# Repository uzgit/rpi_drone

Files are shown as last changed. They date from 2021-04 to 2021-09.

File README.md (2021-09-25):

# Raspberry Pi Drone

This is designed for a Navio2 + RPi flight controller and a power system similar to the [DJI Snail](https://www.dji.com/snail) with a 3S (11.1V) LiPo. It is a modified version of the drone found [on Thingiverse here](https://www.thingiverse.com/thing:2269010).

It is particularly good for scenarios with potentially rough landings, as it is flexible enough to ragdoll a bit, while being strong enough to fly nicely.

## Initialization (if you want to edit or re-generate files):
* Install OpenSCAD: `sudo apt-get install openscad`
* Clone the repo to your computer.
* Run the `./build.sh` script (make sure you have OpenSCAD installed or else this step will obviously not work).

## Printing (drone with gimbal):

Print Item | Quantity | File | Image
:-: | :-: | :-: | :-: |
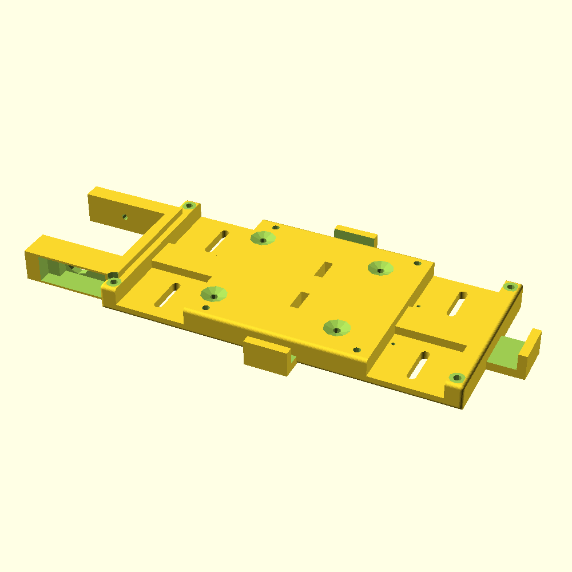
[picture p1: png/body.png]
Body | 1 | `stl/body.stl` | 
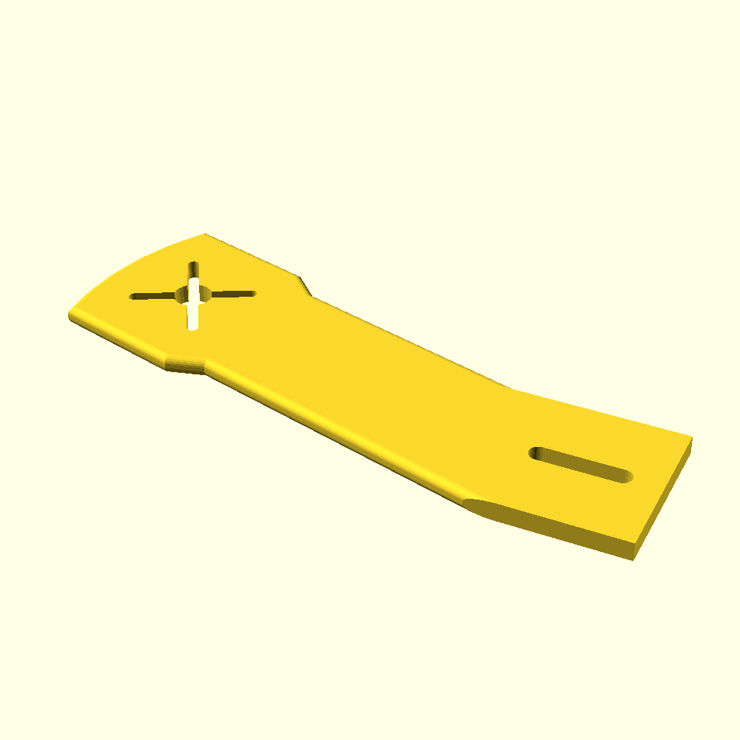
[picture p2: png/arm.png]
Arms | 4 | `stl/arm.stl` | 
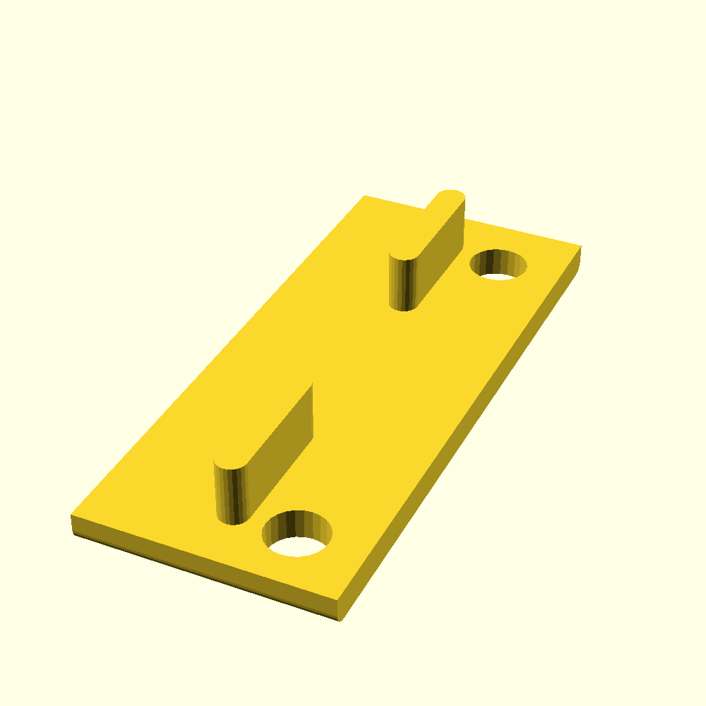
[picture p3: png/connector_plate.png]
Connector plates | 2 | `stl/connector_plate.stl` | 
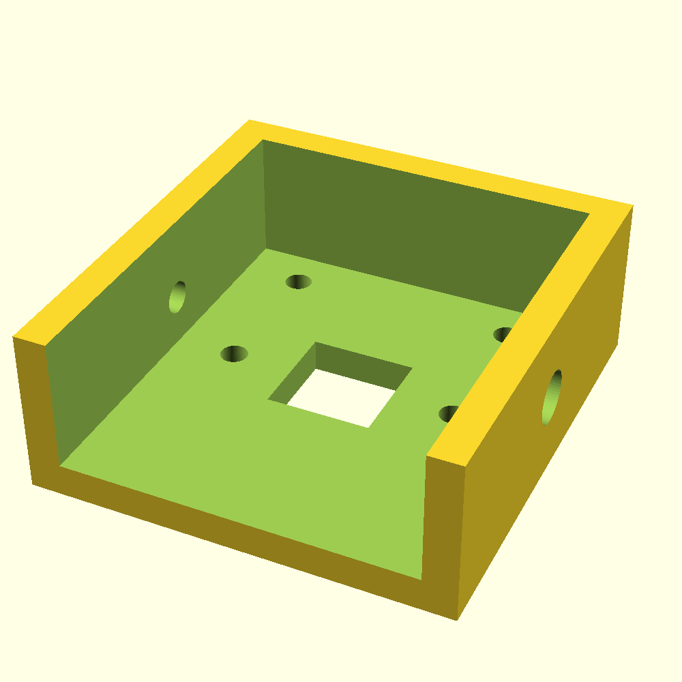
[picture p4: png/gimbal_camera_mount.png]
Camera mount | 1 | `stl/gimbal_camera_mount.stl` | 
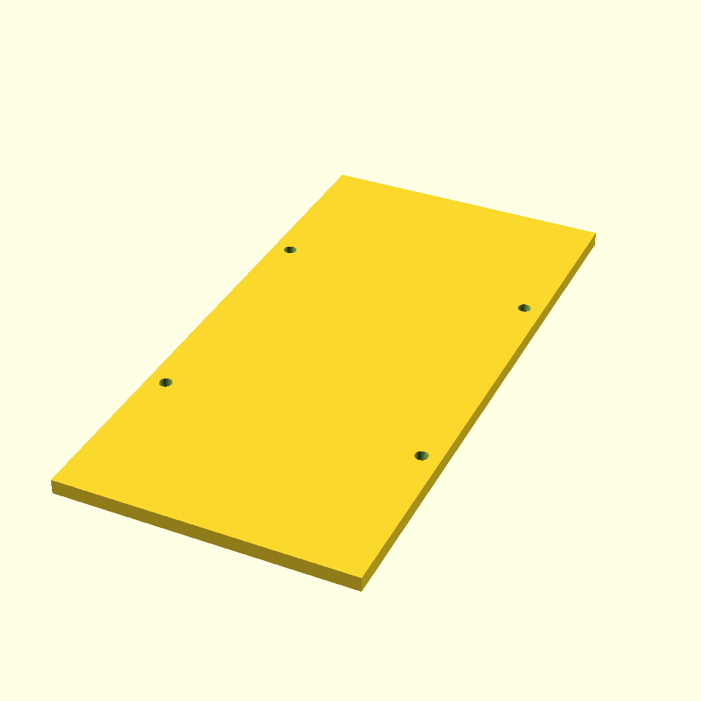
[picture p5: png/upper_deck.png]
Upper deck | 1 | `stl/upper_deck.stl` | 

## Assembly:
* Put one arm in each slot from the underside, angling them away from the center of the drone body.
* Connect the arms by pressing tab from the connector plates into the holes in the arms and the corresponding holes in the body. (You may need a [vice](https://www.google.com/search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) for this. Make sure to do it slowly in order not to break anything.)
* Drill a hole through the connector plate and put a short M3 bolt through it with a nut for security.
* If using a snail propulsion system, you will need to increase the size of the slots in the arms for the required mounting screws. You can do this with a dremel or drill and a slightly larger bit. (This will eventually need to be fixed in the design itself, but is ok for now.)

## Parts List:
### Flight Controller:
* [1 x Raspberry Pi 4](https://www.raspberrypi.org/products/raspberry-pi-4-model-b/)
* [1 x Navio2 with full 433MHz telemetry radio + GPS + power module](https://navio2.emlid.com/)
* [1 x 40-pin GPIO extender (straight)](https://pimodules.com/wp-content/uploads/2019/06/40_Pin_Con.jpg)
* [4 x 10 mm male-to-female nylon M3 standoffs](https://ae01.alicdn.com/kf/HTB1ag2aPXXXXXcsXFXXq6xXFXXXz/50PCS-M3-Black-Nylon-Standoff-M3-5-6-8-10-12-15-18-20-25-30.jpg_640x640.jpg)
### Propulsion/Power:
* [1 x DJI Snail](https://www.dji.com/snail)
* [1-2 x 3S (11.1V) lithium polymer battery ~3300mAh](https://hobbyking.com/en_us/turnigy-battery-3300mah-3s-30c-lipo-pack-xt-60.html?___store=en_us)
* [1 x Small power distribution board (with at least 5 outputs)](https://www.amazon.com/LinsyRC-Distribution-Copper-Helicopter-Quadcopter/dp/B08H8GR53G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)
### Peripherals
* [Micro receiver (and corresponding transmitter)](https://www.gravesrc.com/frsky-r-xsr-2-4ghz-16ch-micro-accst-receiver-with-s-bus-and-cppm.html)
* [1 x Raspberry Pi camera module with ribbon cable](https://www.raspberrypi.org/products/camera-module-v2/)
### Miscellaneous
* [1 x XT-60 connector pair](https://www.amazon.com/Amass-Bullet-Connector-Upgrated-Sheath/dp/B074PN6N4K)
* Various nuts and bolts
* Various small wires
* Electrical tape
* Velcro Straps

## Installation:
* Install the Raspberry Pi at the 4 mounting holes in the body, including spacers to separate it from the body. You can identify these holes unambiguously by the fact that they are the only 4 screw holes that line up with the holes in the Raspberry Pi. Install 4 x ~20mm M3 [countersink screws](https://m.media-amazon.com/images/I/41OX-HUqUYL.jpg) from the bottom up, and install the Raspberry Pi with the USB hub facing forward.
* Plug the camera ribbon cable into the Raspberry Pi's camera port.
* Install a 40-pin header extension on the GPIO rail of the Raspberry Pi, and install 4 x ~10mm standoffs on the 4 RPi mounting screws.
* Install the Navio2 on the Raspberry Pi, with the GPIO pins fitting into the Navio2 GPIO sockets, with M3 washers on top to keep it tight against the standoffs. Run the camera ribbon cable through the slot in the Navio2.
* Plug the GPS antenna into the antenna slot on the Navio2.
* Install the motors into the arms using the (presumably included with your motors) mounting screws. (Don't install the propellers until the very end!)
* Solder the ESC terminals to the power distribution board.
* Install the [power distribution board](https://www.dronetrest.com/uploads/db5290/original/2X/0/03304f2ce1f00f086263f404fa10f85d59372267.jpg) at the rear of the drone body with wood screws.
* Tape the ESCs in the holders on the sides and rear of the body. The front left motor's ESC is on the left side, the front right motor's ESC is on the right side, and the two back motors' ESCs are mounted in the same mount at the back.
* Install the Raspberry Pi camera module into the camera mount using M2 Allen head machine screws. (Be careful when tightening down - do not tighten too hard, and avoid touching the electronics on the rear of the camera module.) The lens of the camera fits into the square in the camera mount.
* Place the camera mount into its place at the front of the drone body.
* Insert the micro servo into its place at the front right of the drone body, press its head into the hole in camera mount, and install the servo with wood screws. Do not over-tighten - you can easily strip the screw hole.
* Install a 12mm M3 machine screw into the front left of the drone body while ensuring that the camera mount is locked onto the servo.
* Plug the free end of the camera's ribbon cable into the camera module.
* Screw a machine screw into each of the holes for mounting the upper deck (from the bottom up), and attach a 30 mm standoff on the other end.
* Align the upper deck to the standoffs and screw in again from the top.
* Tape a strap of velcro to the top of the battery, and tape the other side to the bottom of the drone body, so that the battery sticks to the drone.
* Run another velcro strap underneath the Raspberry Pi and all the way around the bottom of the battery. Stick it to itself.
* Tape the micro receiver to the outermost/rearmost side of the rear ESC mount, with the antennae facing down away from the propellers. Connect the receiver's SBus out pin to the Navio2's SBus in pin.
* Plug the 433 MHz telemetry radio into one of the USB ports on the Raspberry Pi, and tape it to the top of the upper deck using electrical tape or double sided tape.
* Tape the GPS antenna to the upper deck.

## Flight Control Software Setup
* Follow steps for installing the Emlid Raspbian OS on the Raspberry Pi and for setting up the flight control software.
* Calibrate all sensors and other systems.
* Ensure motors are spinning the correct way. [ArduPilot motor layout.](https://ardupilot.org/copter/docs/connect-escs-and-motors.html) [PX4 motor layout](https://dev.px4.io/master/en/airframes/airframe_reference.html)
* Ensure correct flight controller orientation using the HUD in some ground control station software such as [QGroundControl](https://docs.qgroundcontrol.com/master/en/getting_started/download_and_install.html).
* Ensure that when you pitch forward, the back motors rev up, and that the front motors rev up when you pitch back.
* Ensure that when you roll right, the left motors rev up, and that the left motors rev up when you roll left.
* Ensure that the counterclockwise motors rev up when you yaw right, and vice versa.
* Install the propellers.

# Disclaimer: Add/subtract components, installation steps, etc. as needed, using common sense. Please use common sense.

# Still need to find some solution for legs in the drone body (maybe 3d printing, but probably not a good idea...)

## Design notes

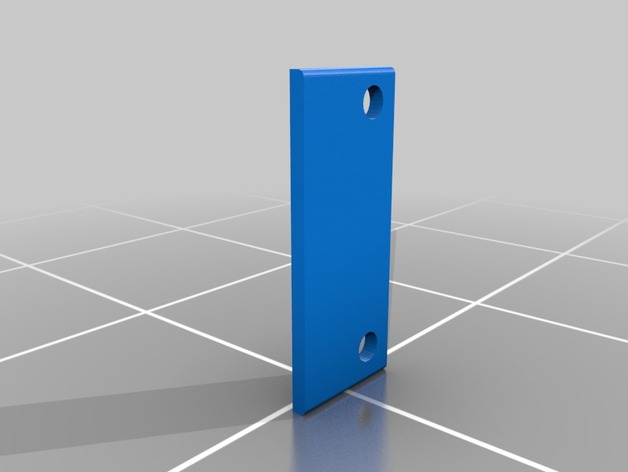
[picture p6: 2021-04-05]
Raspberry_Pi_Drone_/images/18b66b4c66508de75e8b7acbb4b0b68c_preview_featured.jpg

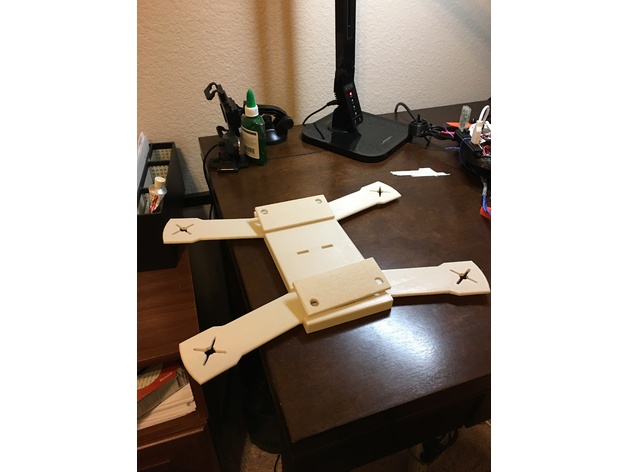
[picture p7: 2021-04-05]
Raspberry_Pi_Drone_/images/b3ce652977a37e82d953b65460e3e9b5_preview_featured.jpeg

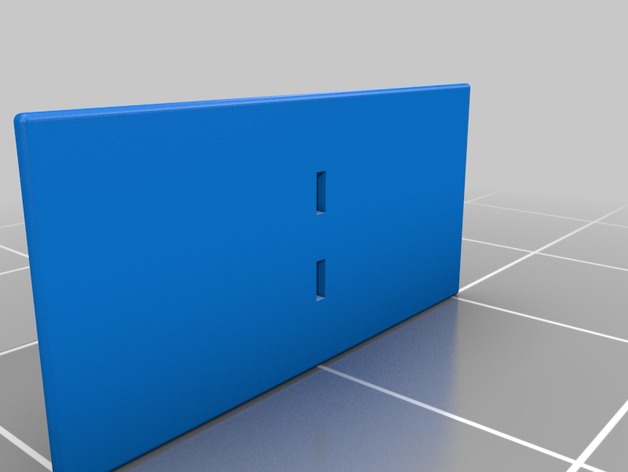
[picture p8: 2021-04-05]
Raspberry_Pi_Drone_/images/03b6a9fba97699c6382648f625db19b3_preview_featured.jpg

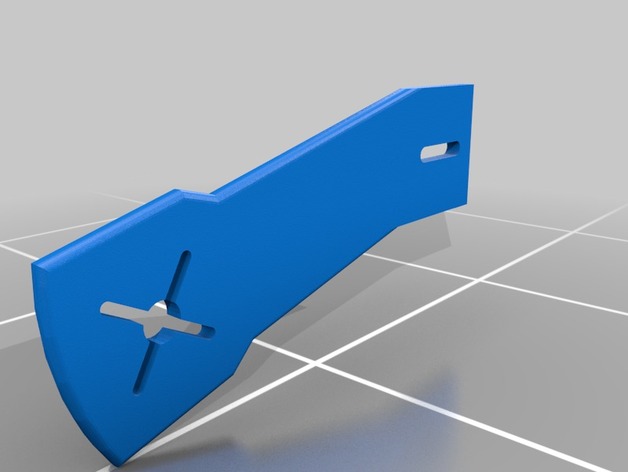
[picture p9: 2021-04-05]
Raspberry_Pi_Drone_/images/210da7942ddf020327a41cb0e29e2601_preview_featured.jpg

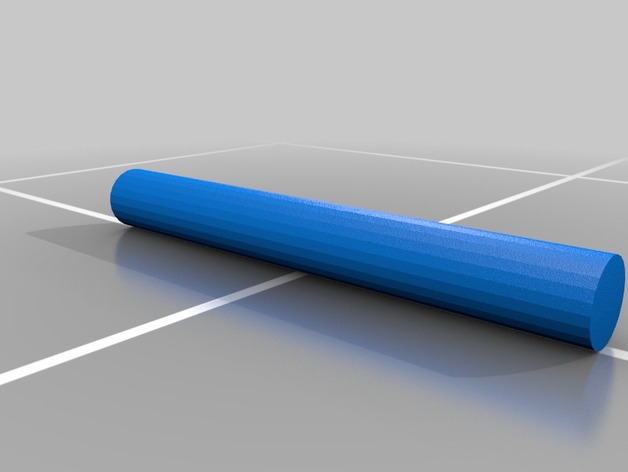
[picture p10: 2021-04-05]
Raspberry_Pi_Drone_/images/7d9828fbd767a6320e98f4d874a620cc_preview_featured.jpg

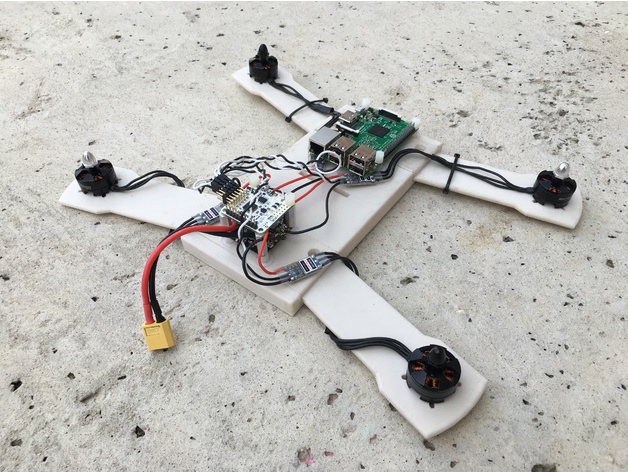
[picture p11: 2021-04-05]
Raspberry_Pi_Drone_/images/1e9882656a89c5c9ec87b1fc31a420ad_preview_featured.jpeg

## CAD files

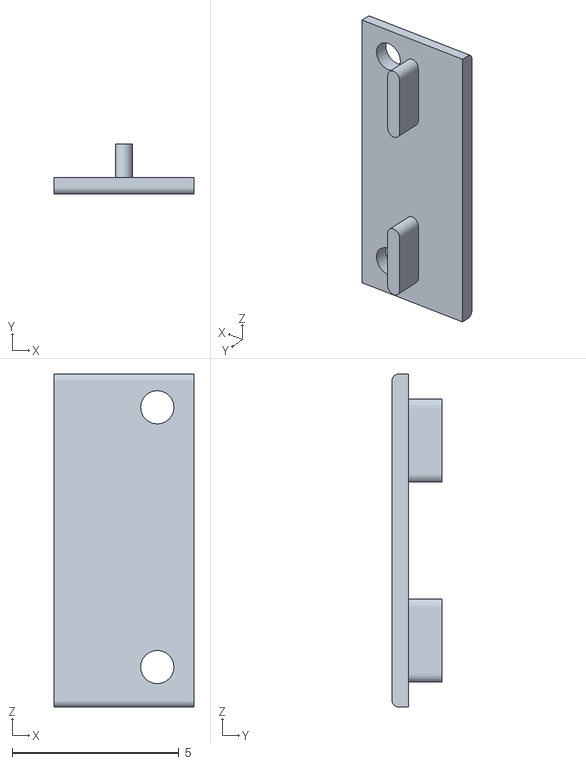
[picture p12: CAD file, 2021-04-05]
Raspberry_Pi_Drone_/files/topplate.stl
4.20 x 1.50 x 10.0

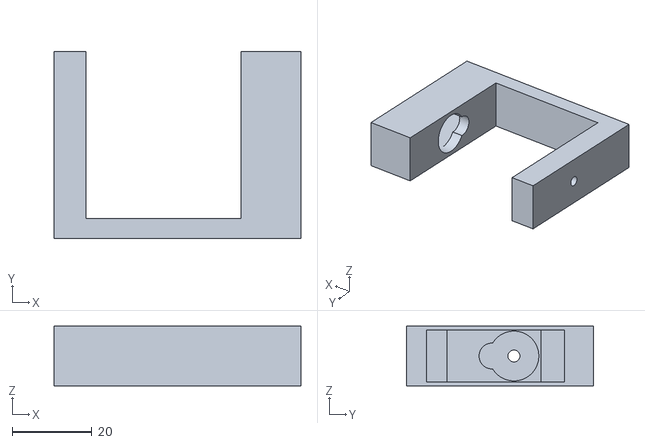
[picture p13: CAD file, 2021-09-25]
stl/gimbal_base.stl
62.0 x 47.0 x 15.0

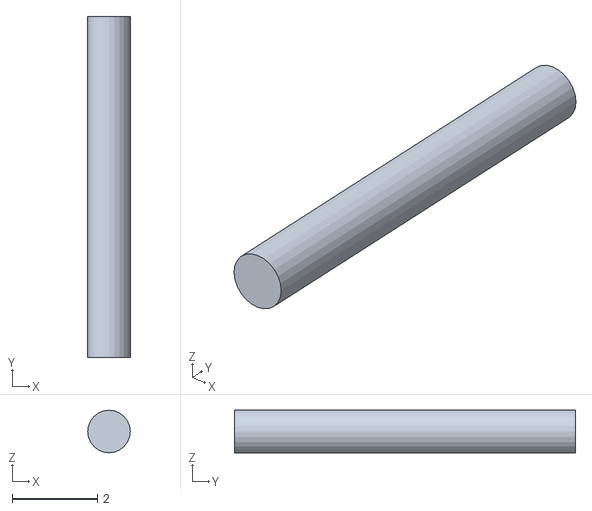
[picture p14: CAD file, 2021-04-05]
Raspberry_Pi_Drone_/files/peg.stl
1.00 x 8.00 x 1.00

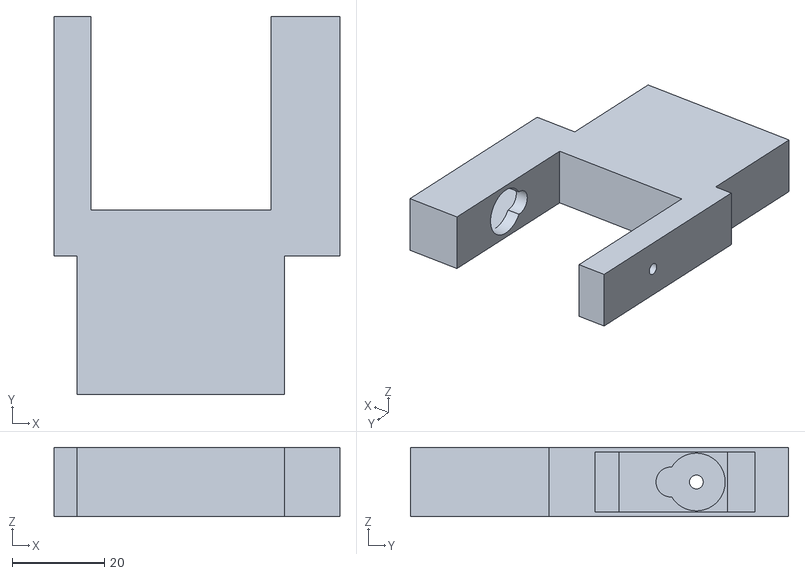
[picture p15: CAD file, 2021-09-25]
stl/gimbal_base_standalone.stl
62.0 x 82.0 x 15.0

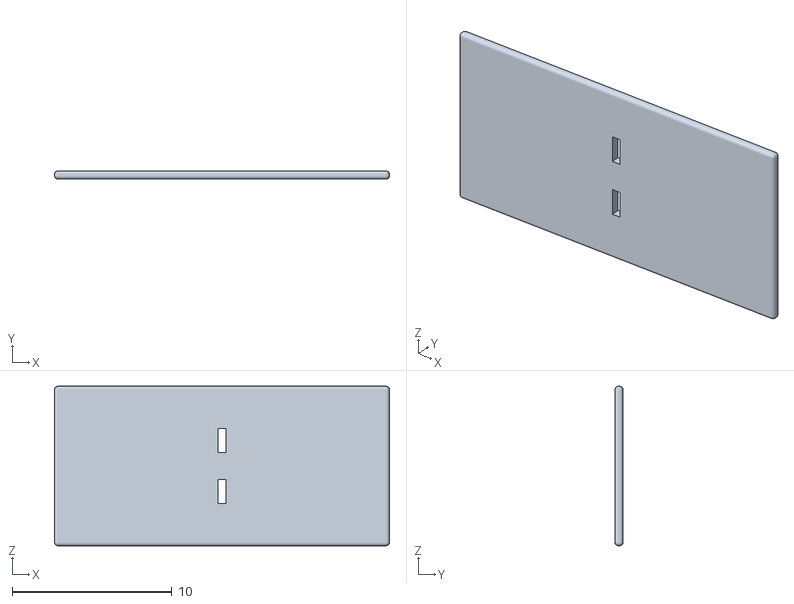
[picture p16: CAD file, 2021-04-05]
Raspberry_Pi_Drone_/files/top.stl
21.0 x 0.5 x 10.0

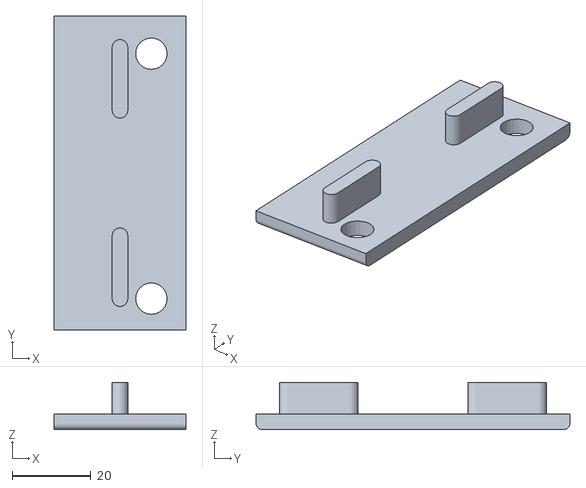
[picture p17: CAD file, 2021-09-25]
stl/connector_plate.stl
33.6 x 80.0 x 12.0

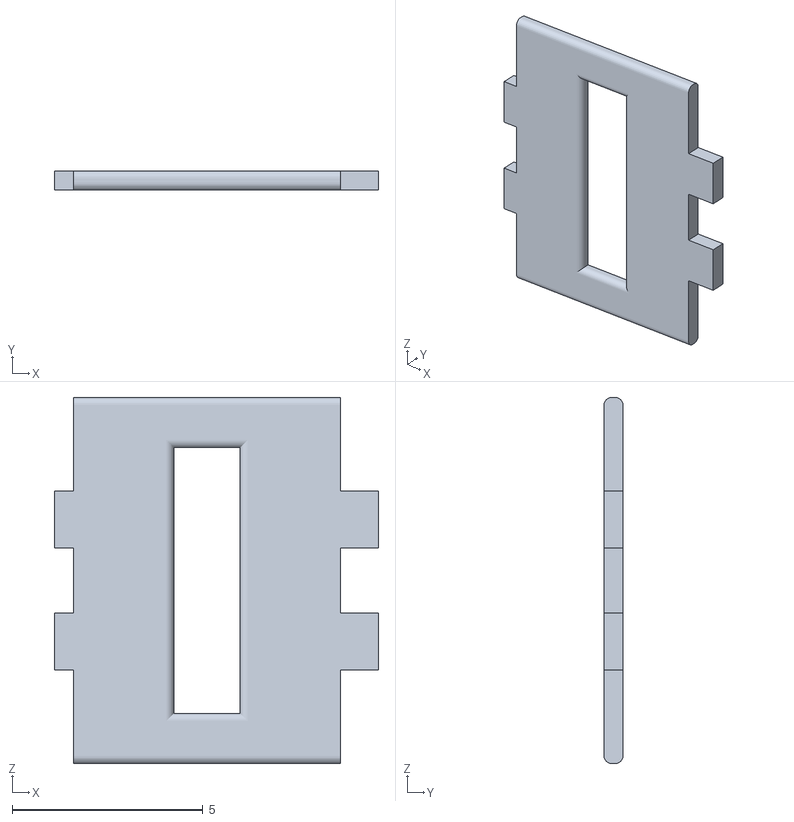
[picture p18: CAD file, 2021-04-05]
Raspberry_Pi_Drone_/files/spacerplate.stl
8.50 x 0.5 x 9.60

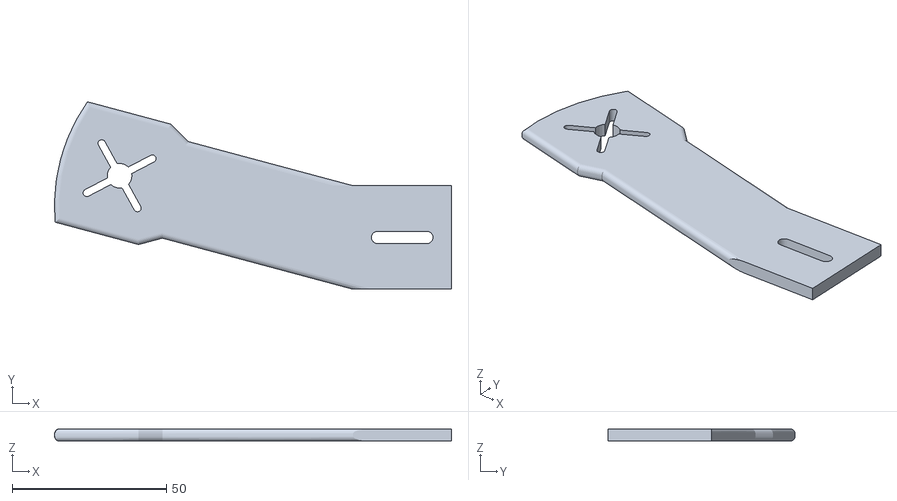
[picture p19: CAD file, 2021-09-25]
stl/arm.stl
128.8 x 60.8 x 4.00

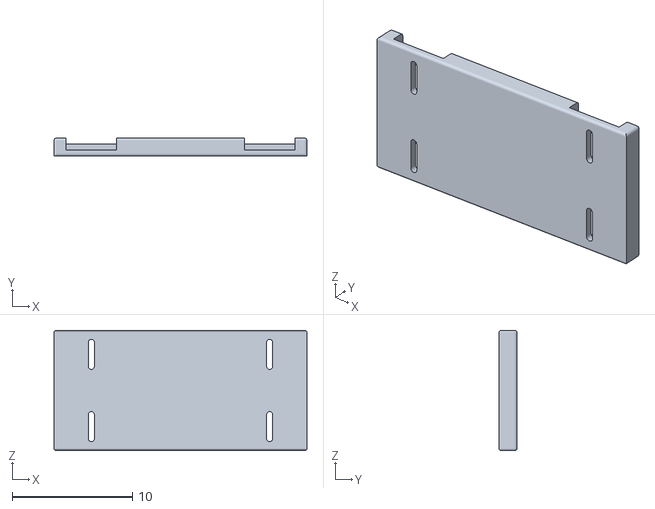
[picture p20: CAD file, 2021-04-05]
Raspberry_Pi_Drone_/files/NIACAM2.body.stl
21.0 x 1.50 x 10.0

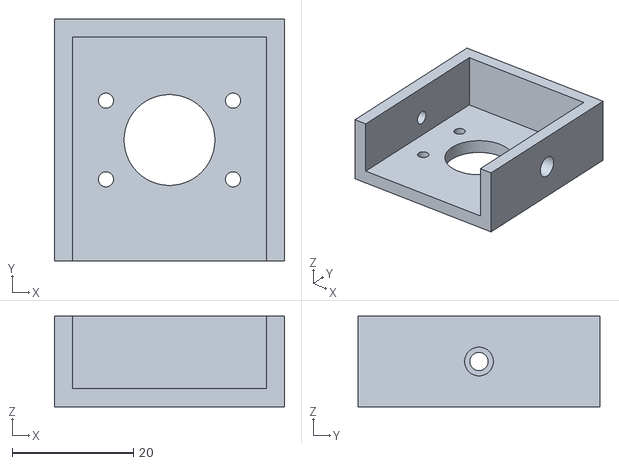
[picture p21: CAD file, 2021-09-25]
stl/fisheye_gimbal_camera_mount.stl
38.0 x 40.0 x 15.0

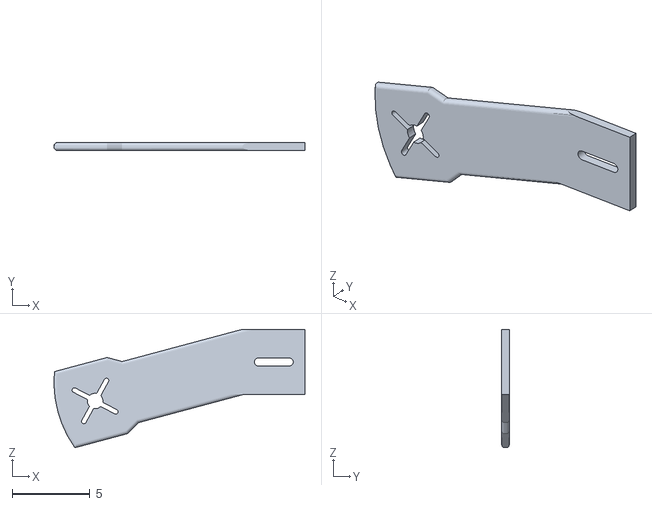
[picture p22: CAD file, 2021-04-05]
Raspberry_Pi_Drone_/files/angled.stl
16.1 x 0.5 x 7.60

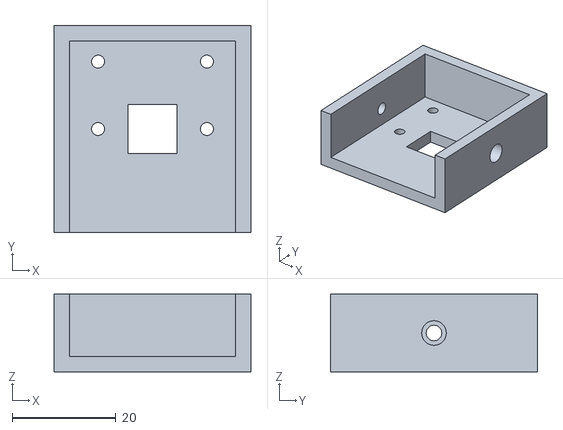
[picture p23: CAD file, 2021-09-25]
stl/gimbal_camera_mount.stl
38.0 x 40.0 x 15.0

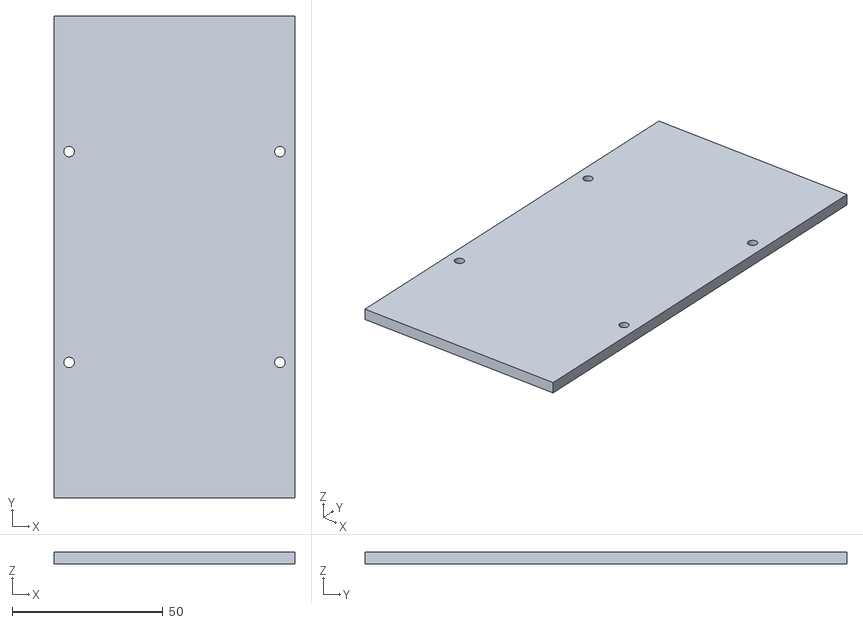
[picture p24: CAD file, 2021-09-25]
stl/upper_deck.stl
80.0 x 160.0 x 4.00

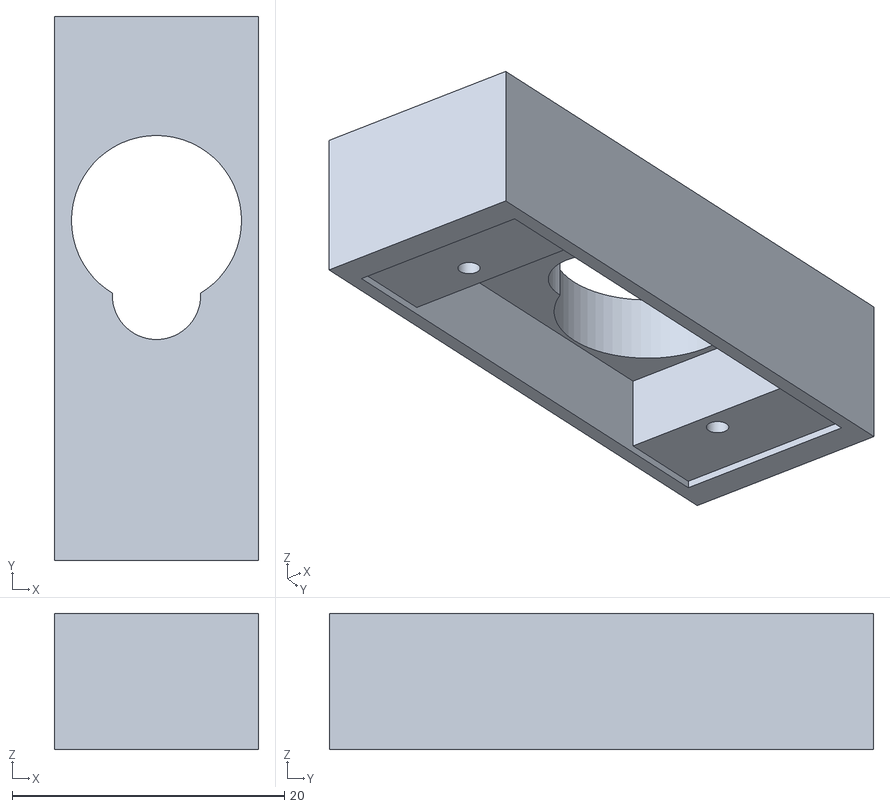
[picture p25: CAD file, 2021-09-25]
stl/servo_mount_test.stl
15.0 x 40.0 x 10.0

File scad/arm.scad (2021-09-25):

scale([8,8,8])
rotate([90,0,0])
import("../Raspberry_Pi_Drone_/files/angled.stl");

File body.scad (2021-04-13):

include <lib/rpi.scad>
include <lib/rpi_tilt_gimbal_lib.scad>

$fn = 60;

module stand()
{
    width = 2;
    translate([-width/2, 0, 0])
    cube([width, 10, 5]);
}

module rear_speed_controller_mount()
{
    length = 17;
    width = 20;
    height = 12;
    difference()
    {
        union()
        {
            translate([-width/2, 0, -height])
            cube([width, length, height]);
        }
        union()
        {
            translate([-width/2, 4, -height])
            cube([width, length-4, height - 4]);
        }
    }
}

speed_controller_mount_x_offset = 38;
speed_controller_mount_y_offset = -85;

module speed_controller_mount()
{
    length = 20;
    width = 10;
    height = 12;
    
    difference()
    {
        union()
        {
            translate([0, -length/2, -height])
            cube([width, length, height]);
        }
        union()
        {
            translate([0, -length/2, -height])
            cube([width-4, length, height - 4]);
        }
    }
}

module power_distribution_board_holes(thickness = 100, screw_hole_diameter = 1.5)
{
    for( x_offset = [-15, 15] )
    {
        for( y_offset = [-15, 15] )
        {
            translate([x_offset, y_offset, -thickness])
            cylinder( d = screw_hole_diameter, h = thickness );
        }
    }
}

module leg_holes(thickness = 20)
{
    clearance = 10;
    
    base_y_offset = -4.5;
    for( x_offset = [-35, 35] )
    {
        for( y_offset = [0, -159] )
        {
            // screw hole
            translate([x_offset, base_y_offset + y_offset, -thickness])
            cylinder(d=4, h=thickness);
            
            // screw head cone
            translate([x_offset, base_y_offset + y_offset, 0])
            rotate([0, 180, 0])
            base_plate_screw_head_cone(screw_head_radius = 4);
        }
    }
}

module leg_hole_clearance(thickness = 12)
{
    clearance = 10;
    
    base_y_offset = -4.5;
    for( x_offset = [-35, 35] )
    {
        for( y_offset = [0, -159] )
        {
            // clearance
            translate([x_offset, base_y_offset + y_offset, -thickness - clearance])
            cylinder(d=9, h=clearance);
        }
    }
}

module body()
{
    difference()
    {
        union ()
        {
            translate([40, 0, 0])
            rotate([-90, 0, 90])
            scale([8, 8, 8])
            import("./Raspberry_Pi_Drone_/files/NIACAM2.body.stl");
            
            translate([- base_width / 2, y_offset, -base_thickness])
            base();
            
            translate([speed_controller_mount_x_offset, speed_controller_mount_y_offset, 0])
            speed_controller_mount();
            
            translate([-speed_controller_mount_x_offset, speed_controller_mount_y_offset, 0])
            rotate([0, 0, 180])
            speed_controller_mount();
            
            translate([0, -178, 0])
            rear_speed_controller_mount();
            
            tilt_gimbal_base();
        }
        union()
        {
            leg_holes();
            leg_hole_clearance();
            
            translate([28, -110, 0])
            rotate([0, 0, 90])
            raspberry_pi_holes(thickness = 12, screw_hole_diameter = 4);
            
            translate([0, -143.5, 0])
            power_distribution_board_holes();
        }
    }
}

body();

//tilt_gimbal_camera_mount();

//            translate([- camera_mount_width / 2, base_support_length + y_offset + 1, -base_thickness])
////translate([- camera_mount_width / 2, camera_mount_length / 2 + 25, 0])
//            camera_mount();

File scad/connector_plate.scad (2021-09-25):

scale([8,8,8])
rotate([90,0,0])
import("../Raspberry_Pi_Drone_/files/topplate.stl");

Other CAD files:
stl/body.stl
scad/body.scad
legacy/old.rpi_tilt_gimbal_lib.scad
legacy/orig.rpi_tilt_gimbal_lib.scad
legacy/rpi_tilt_gimbal.scad
legacy/upper_deck.scad
scad/fisheye_gimbal_camera_mount.scad
scad/gimbal_base_standalone.scad
scad/gimbal_camera_mount.scad
scad/servo_mount_test.scad
scad/upper_deck.scad

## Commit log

2021-04-05 Initial commit. Raspberry_Pi_Drone taken from https://www.thingiverse.com/thing:2269010
    [NIACAM2.body.stl, angled.stl, peg.stl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]
2021-04-05 Added gimbal to body
    [body.scad, body.stl, camera_mount.stl]
2021-04-05 Made the camera mount a bit farther away from the body.
    [body.scad, camera_mount.stl]
2021-04-08 Added mounts for speed controllers.
    [body.scad, body.stl, camera_mount.stl]
2021-04-12 Changed form of gimbal so that the servo controls it directly, instead of with a control arm.
    [body.stl, camera_mount.stl, rpi_tilt_gimbal.scad]
2021-04-12 Added missing files.
    [old.rpi_tilt_gimbal_lib.scad, orig.rpi_tilt_gimbal_lib.scad, rpi_tilt_gimbal.scad]
2021-04-12 Increased servo indent.
    [body.scad]
2021-04-13 Moved leg holes to center them better. Added leg clearance.
    [body.scad]
2021-04-13 Added a script to build things more easily.
    [body.scad, gimbal_base.scad, gimbal_camera_mount.scad]
2021-04-13 Reduced screw hole size for rpi and legs from 4mm to 3.5mm. Increased ESC mount size.
    [body.scad]
2021-04-14 Added clearance to micro_servo_void and created a test mount.
2021-04-14 Fixed location/configuration for servo_mount_test in relation to build.sh.
2021-04-14 Added forgotten servo mount test file.
    [servo_mount_test.scad]
2021-04-24 Added upper deck and some modified RPi functions.
    [upper_deck.scad]
2021-05-07 Added fisheye holes and mount.
    [fisheye_gimbal_camera_mount.scad]
2021-09-02 Added a standalone gimbal.
    [gimbal_base_standalone.scad]
2021-09-03 Fixed standalone STL generation.
    [gimbal_base_standalone.scad]
2021-09-09 Rotated body for easier positioning in Prusa Slicer.
    [body.scad]
2021-09-09 Added more holes and a flat upper deck.
    [body.scad, upper_deck.scad]
2021-09-25 Added specific STLs for arms and connector plates. added raw PNGs and STLs for ease.
    [arm.scad, arm.stl, body.scad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]
